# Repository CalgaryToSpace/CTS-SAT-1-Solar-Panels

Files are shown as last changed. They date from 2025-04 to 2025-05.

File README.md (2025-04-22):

# CTS-SAT-1-Solar-Panels
Solar panel PCB designs for the CTS-SAT-1 3U cubesat

## Overview
* 4x COTS 2U solar panels are the main power generation for the satellite.
* As a proof of concept, the following panels are manufactured in-house:
    * 2x 1.25U panels
    * 1x 1.0U panel
* Each panel has backflow blocking diodes and shadow-protection diodes.

## 1.25U Solar Panel

* 30 cells, in a 6S5P configuration (6 cells in each string, then joined in parallel).

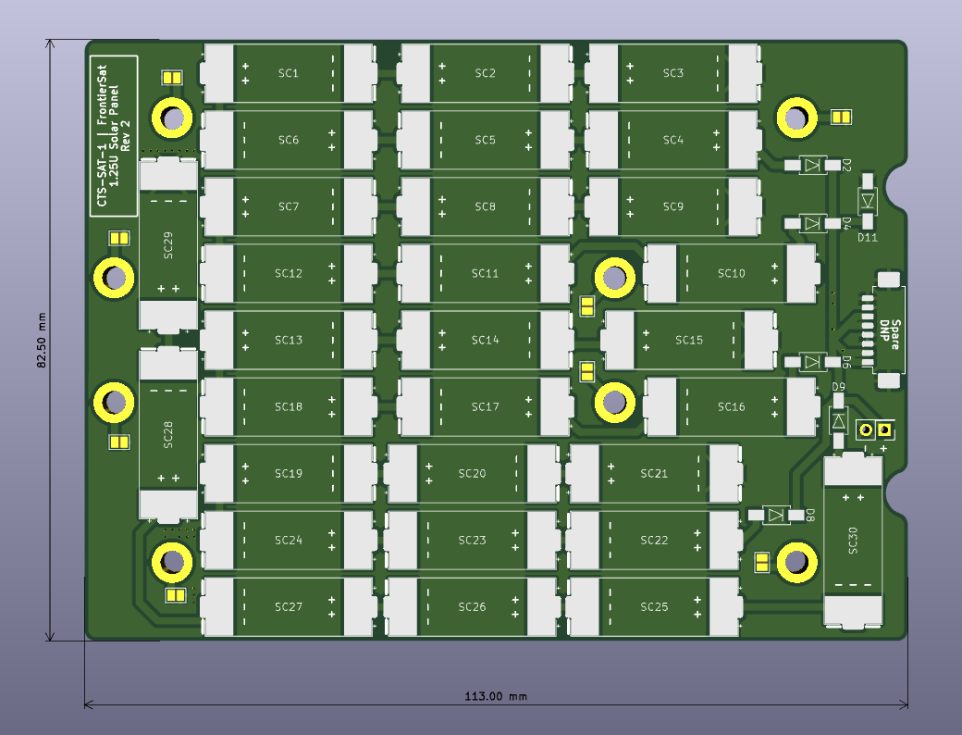
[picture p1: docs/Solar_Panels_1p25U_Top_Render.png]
1.25U Solar Panel - Top


## Bill of Materials
* PMEG10020AELPX diode in a SOD128 package
* [AA-DUCT 902 Silver Epoxy Adhesive](https://atomadhesives.com/aa-duct-902-silver-epoxy-adhesive-electrically-conductive-room-temp-curing-air-dr/)

## Solar Panel Assembly Steps
Work in the Laminar Flow Table with proper ESD protection. Wear gloves. Be careful with fragile cells.

1. Clean solar panel with isopropyl alcohol.
2. Boil some water.
3. Put epoxy in hot water for 10 minutes.
4. Massage epoxy in pouch.
5. Get out the solar cells.
6. Apply some epoxy to solar panel pads.
7. Take a picture of the application for reference on future applications.
8. Use the suction tool to place solar cells on the panels.
9. Apply pressure by placing a PCB on top of the soldered panel, and placing a 300g mass on top.
10. Wait 24h for epoxy to dry.
11. Solder short wires to the nearby pads, ensuring the solder blobs do not stick out the back side.
12. Inspect the work.
13. The assembly is complete. 

## License
This project is licensed under the [CERN OHL v2 Permissive](https://choosealicense.com/licenses/cern-ohl-p-2.0/) license. We appreciate attribution and links back, but you are free to do what you wish with this project.

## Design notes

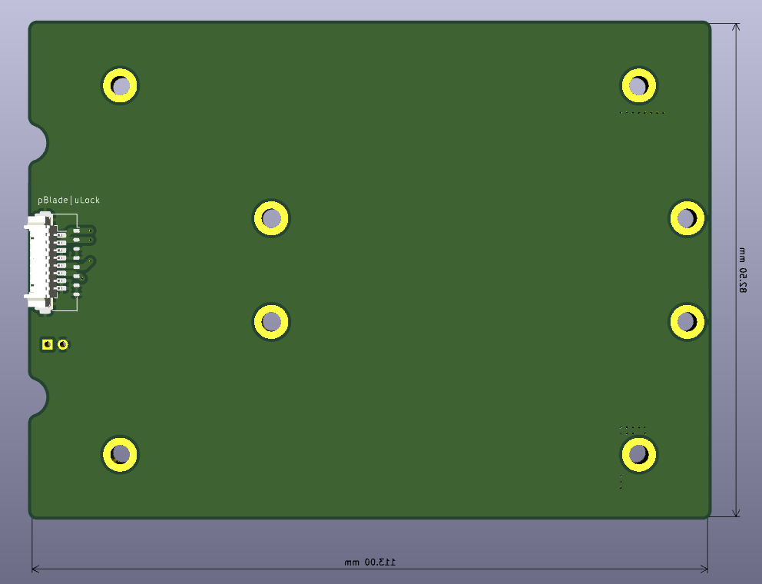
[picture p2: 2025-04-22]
docs/Solar_Panels_1p25U_Bottom_Render.png

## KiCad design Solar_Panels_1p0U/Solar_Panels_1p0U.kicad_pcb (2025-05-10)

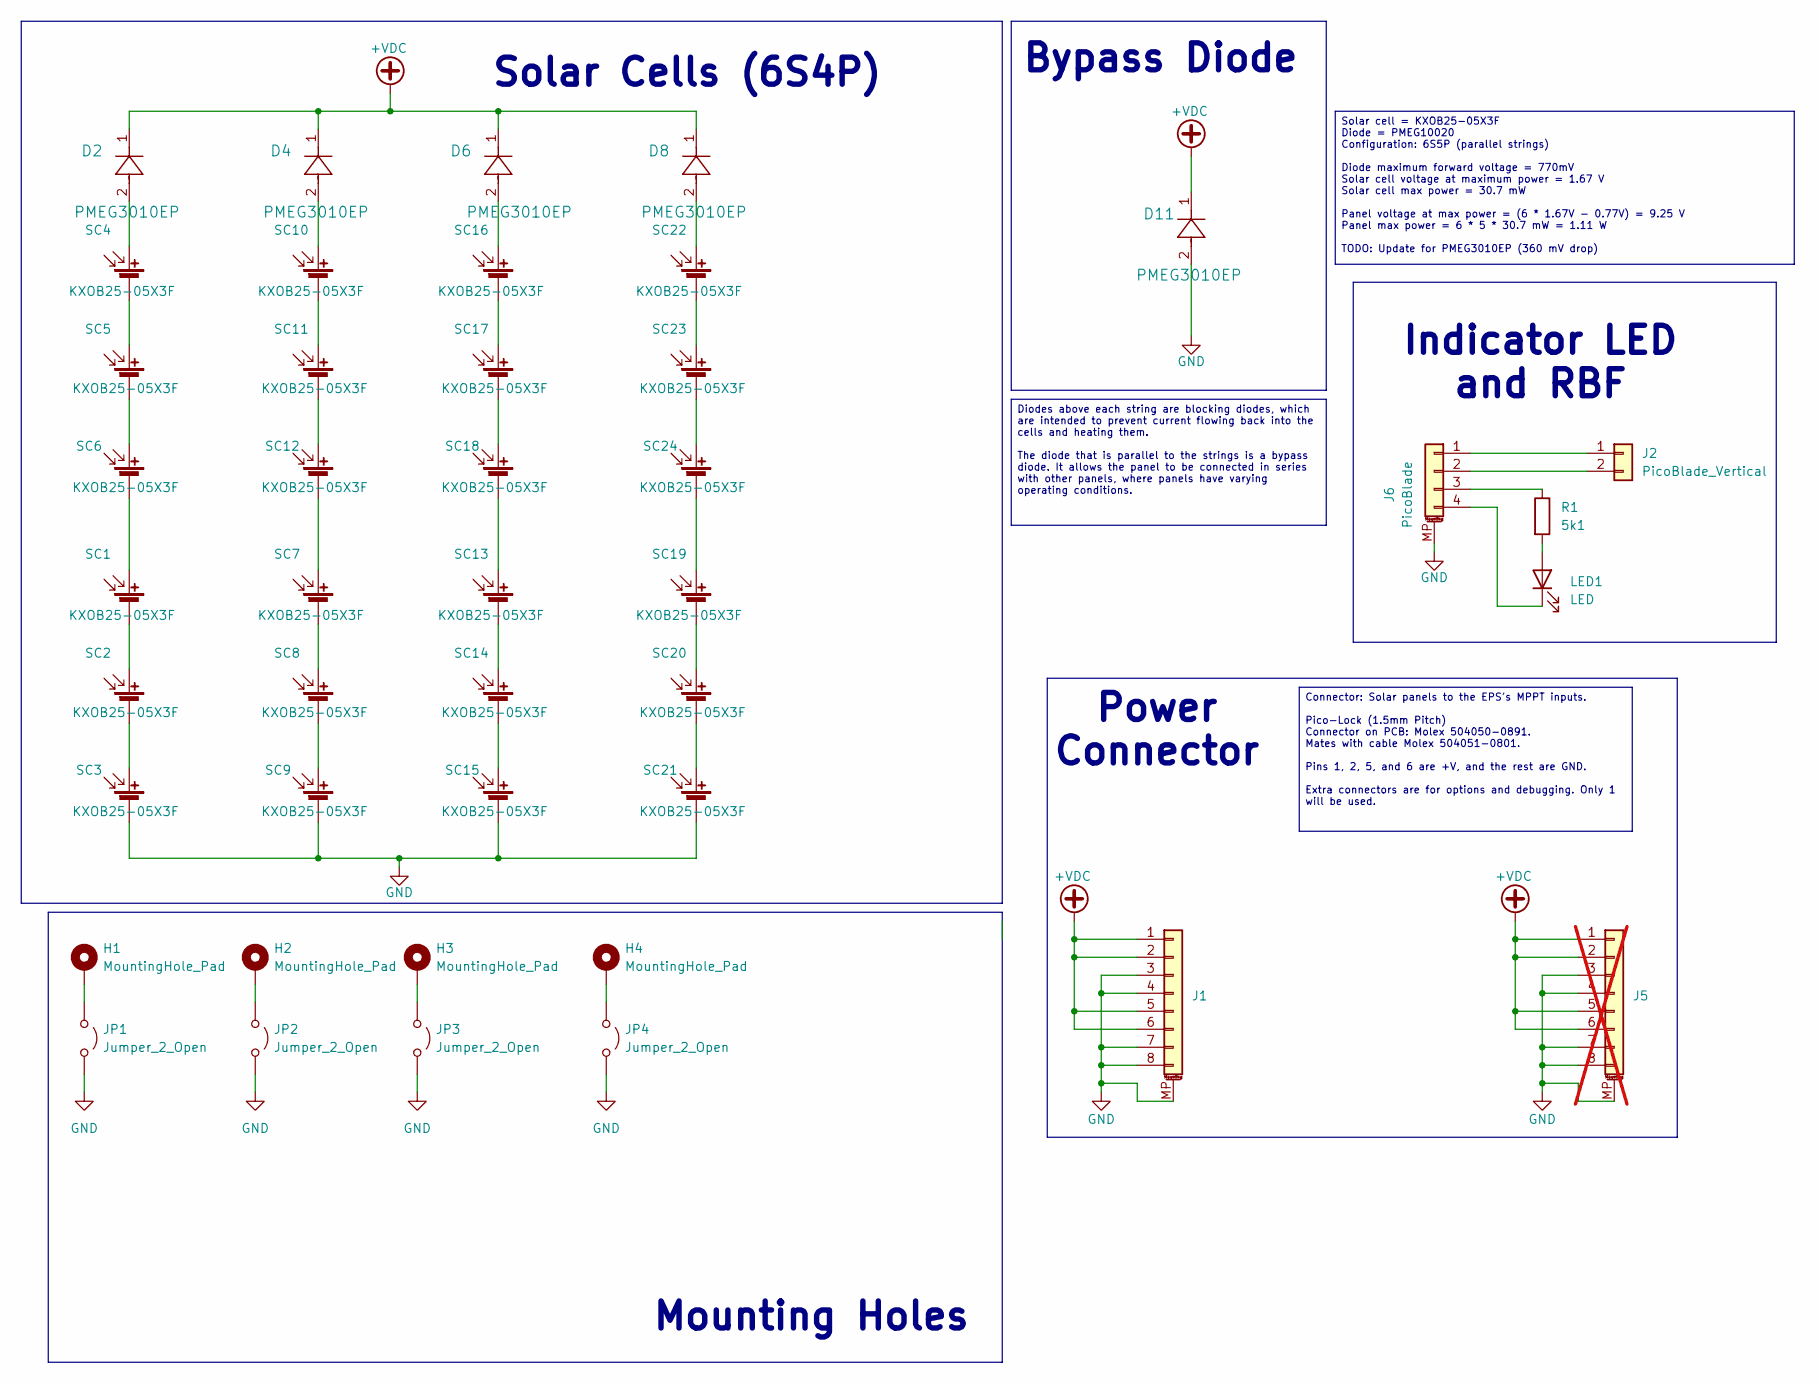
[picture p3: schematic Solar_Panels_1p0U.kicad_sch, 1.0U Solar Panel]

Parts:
D2, D4, D6, D8, D11: PMEG3010EP; PMEG10020AELPX
H1, H2, H3, H4: MountingHole_Pad; MountingHole_3.2mm_M3_DIN965_Pad
J1: Conn_01x08_MountingPin; Molex_PicoBlade_53261-0871_1x08-1MP_P1.25mm_Horizontal
J2: PicoBlade_Vertical; Molex_PicoBlade_53047-0210_1x02_P1.25mm_Vertical
J5: Conn_01x08_MountingPin; Molex_Pico-Lock_504050-0891_1x08-1MP_P1.50mm_Horizontal; not fitted
J6: PicoBlade; Molex_PicoBlade_53261-0471_1x04-1MP_P1.25mm_Horizontal
JP1, JP2, JP3, JP4: Jumper_2_Open; SolderJumper-2_P1.3mm_Open_Pad1.0x1.5mm
LED1: LED; LED_0603_1608Metric_Pad1.05x0.95mm_HandSolder
R1: 5k1; R_0603_1608Metric_Pad0.98x0.95mm_HandSolder
SC1, SC2, SC3, SC4, SC5, SC6, SC7, SC8, SC9, SC10, SC11, SC12, SC13, SC14, SC15, SC16, SC17, SC18, SC19, SC20, SC21, SC22, SC23, SC24: KXOB25-05X3F

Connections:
+VDC: D2.1, D4.1, D6.1, D8.1, D11.1, J1.1, J1.2, J1.5, J1.6, J5.1, J5.2, J5.5, J5.6
GND: D11.2, J1.3, J1.4, J1.7, J1.8, J1.MP (MountPin), J5.3, J5.4, J5.7, J5.8, J5.MP (MountPin), J6.MP (MountPin), JP1.2 (B), JP2.2 (B), JP3.2 (B), JP4.2 (B), SC3.2 (-), SC9.2 (-), SC15.2 (-), SC21.2 (-)
unnamed: J2.1, J6.1
unnamed: J2.2, J6.2
unnamed: J6.3, R1.1
unnamed: J6.4, LED1.1 (K)
unnamed: H1.1, JP1.1 (A)
unnamed: H2.1, JP2.1 (A)
unnamed: H3.1, JP3.1 (A)
unnamed: H4.1, JP4.1 (A)
unnamed: LED1.2 (A), R1.2
unnamed: SC1.1 (+), SC6.2 (-)
unnamed: SC1.2 (-), SC2.1 (+)
unnamed: SC2.2 (-), SC3.1 (+)
unnamed: D2.2, SC4.1 (+)
unnamed: SC4.2 (-), SC5.1 (+)
unnamed: SC5.2 (-), SC6.1 (+)
unnamed: SC7.2 (-), SC8.1 (+)
unnamed: SC8.2 (-), SC9.1 (+)
unnamed: D4.2, SC10.1 (+)
unnamed: SC10.2 (-), SC11.1 (+)
unnamed: SC11.2 (-), SC12.1 (+)
unnamed: SC7.1 (+), SC12.2 (-)
unnamed: SC13.1 (+), SC18.2 (-)
unnamed: SC13.2 (-), SC14.1 (+)
unnamed: SC14.2 (-), SC15.1 (+)
unnamed: D6.2, SC16.1 (+)
unnamed: SC16.2 (-), SC17.1 (+)
unnamed: SC17.2 (-), SC18.1 (+)
unnamed: SC19.1 (+), SC24.2 (-)
unnamed: SC19.2 (-), SC20.1 (+)
unnamed: SC20.2 (-), SC21.1 (+)
unnamed: D8.2, SC22.1 (+)
unnamed: SC22.2 (-), SC23.1 (+)
unnamed: SC23.2 (-), SC24.1 (+)

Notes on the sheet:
Power Connector
Mounting Holes
Bypass Diode
Indicator LED and RBF
Solar Cells (6S4P)
Diodes above each string are blocking diodes, which are intended to prevent current flowing back into the cells and heating them. The diode that is parallel to the strings is a bypass diode. It allows the panel to be connected in series with other panels, where panels have varying operating conditi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
Connector: Solar panels to the EPS's MPPT inputs. Pico-Lock (1.5mm Pitch) Connector on PCB: Molex 504050-0891. Mates with cable Molex 504051-0801. Pins 1, 2, 5, and 6 are +V, and the rest are GND. Extra connectors are for options and debugging. Only 1 will be used.
Solar cell = KXOB25-05X3F Diode = PMEG10020 Configuration: 6S5P (parallel strings) Diode maximum forward voltage = 770mV Solar cell voltage at maximum power = 1.67 V Solar cell max power = 30.7 mW Panel voltage at max power = (6 * 1.67V - 0.77V) = 9.25 V Panel max power = 6 * 5 * 30.7 mW = 1.11 W T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

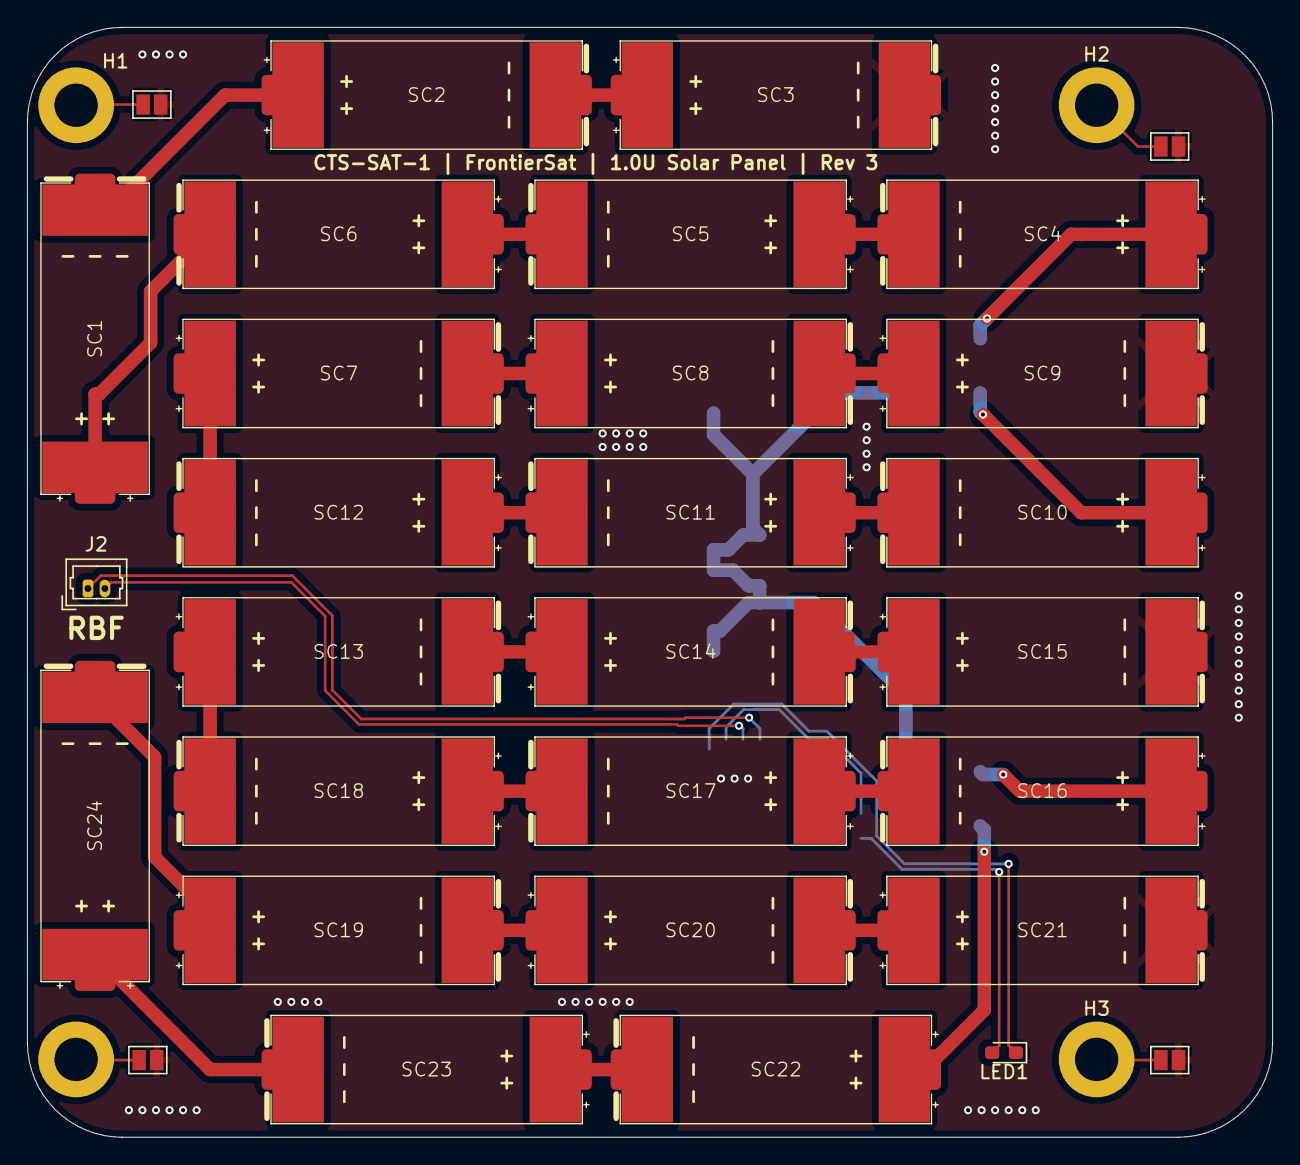
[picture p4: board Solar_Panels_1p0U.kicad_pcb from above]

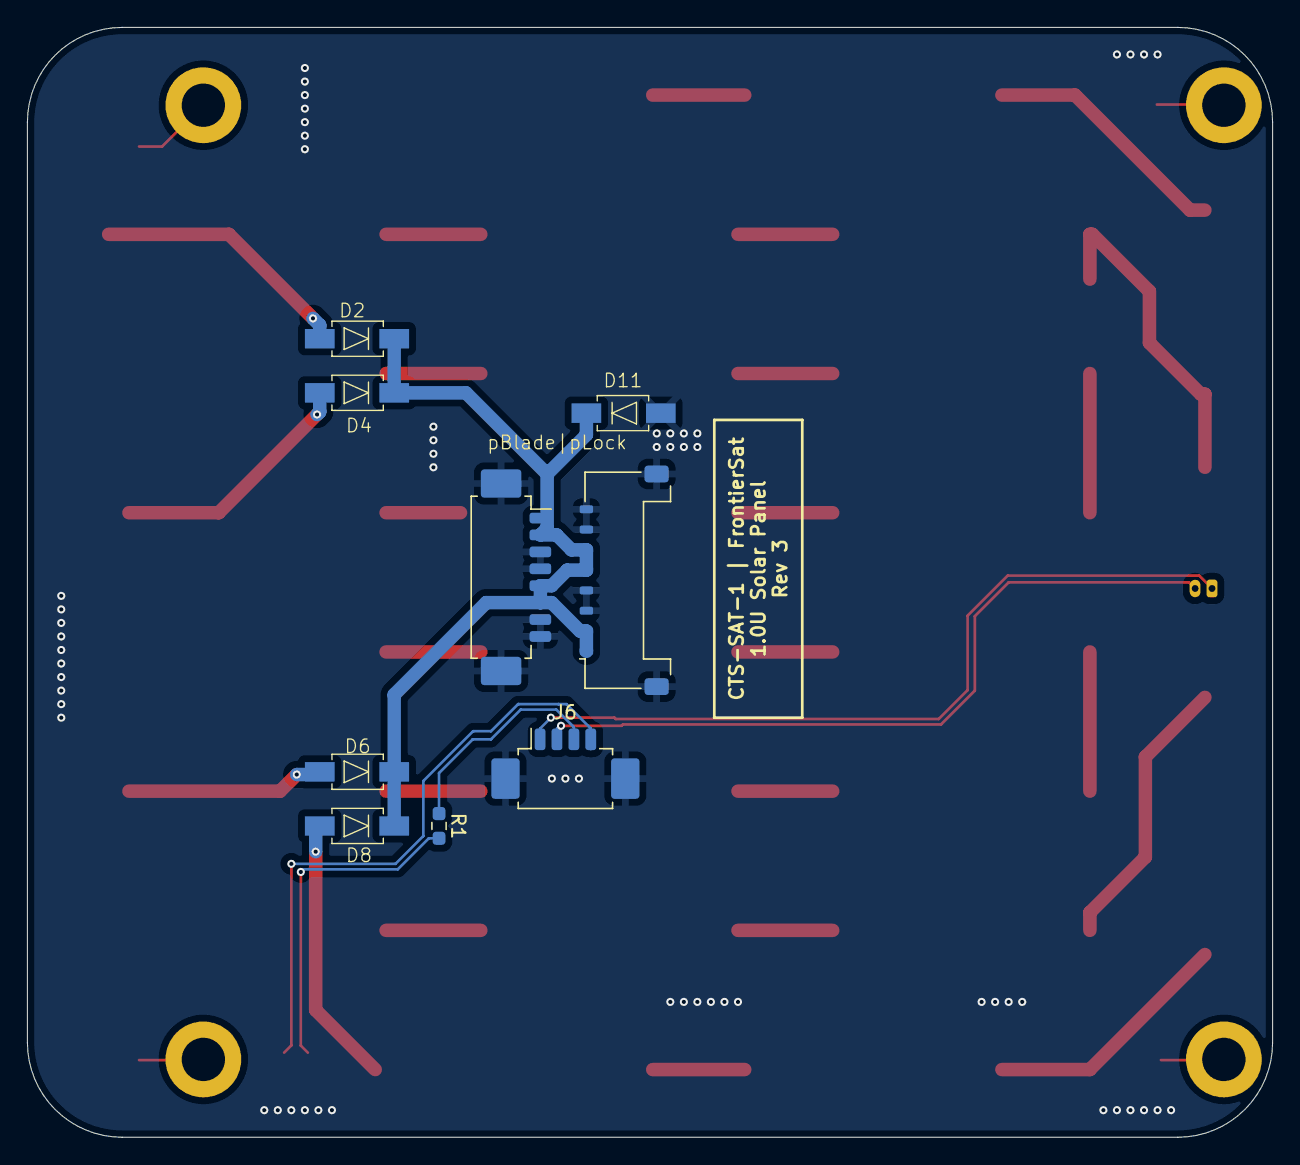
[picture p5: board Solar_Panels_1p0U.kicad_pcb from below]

Board: 2 copper layers, 92.0 x 82.0 mm, 43 parts (9 on the bottom side), 35 nets.

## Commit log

2024-01-16 Add a couple notes to README
2024-07-13 Add KiCAD Gitignore
2024-07-13 Initial Design
    Design before being revised by Parker and Dr. Nacho
    [Solar Panels.kicad_pcb, Solar Panels.kicad_sch]
2024-07-17 Updated Initial Panels
    Updated a bit of the routing before Parker and Nacho takes a look at it. Put the connector on the inside.
    [Solar Panels.kicad_pcb]
2024-07-17 Initial Panels Revision
    Changed the Solar Panels to adjust to structural needs.
    [Solar Panels.kicad_pcb]
2024-07-17 Updated Solar Panels
    Revised to fit Brett's preferences.
    [Solar Panels.kicad_pcb]
2024-07-24 Modifications For 2U Panels
    Made structural modifications to suit Brett's structure and tried to improve the PCB board based on Parker's suggestions. Schematic is extremely wonky right now but will try to fix it ASAP.
    [Solar Panels.kicad_pcb, Solar Panels.kicad_sch]
2024-07-30 Diodes changes and adjusted schematic.
    Made the diode changes based off Parker's suggestions and fixed the schematic. Comments are now included within the schematic.
    [Solar Panels.kicad_pcb, Solar Panels.kicad_sch]
2024-07-31 Quick Adjustments to Schematic and Routing
    Adjusted so there's only one bypass diode for the entire panel. Made changes to the routing as well.
    [Solar Panels.kicad_pcb, Solar Panels.kicad_sch]
2024-08-06 Routed the PCB after the Footprint Adjustments
    Routed the PCB after making adjustments to the TriSolX footprint.
    [Solar Panels.kicad_pcb, Solar Panels.kicad_sch]
2024-08-07 PDF Schematic
    Created a PDF Schematic for review.
2024-08-07 Added Vdc Info
    Quick schematic change to indicate vdc.
    [Solar Panels.kicad_sch]
2024-08-07 more information added to schematic
    added more info for the voltages
    [Solar Panels.kicad_sch]
2024-08-10 Refined Simons 2u
    I tried refining Simons design a bit and aligned the holes/dimensions to the most current frame version.
    Looking good on the structural side. Think we just need a last electrical review then should be ready to order.
    [Solar Panels.kicad_pcb]
2024-08-17 Small schematic cleanup
    [Solar Panels.kicad_sch]
2024-08-17 Improve footprints, layout, routing
    [Solar Panels.kicad_pcb, Solar Panels.kicad_sch]
2024-08-24 Changed the footprint of the solar panels a tiny bit
    Changed the footprints so that the keepout zone is a tiny bit bigger.
    [Solar Panels.kicad_pcb]
2024-08-24 Adjusted some placements and the footprint
    Made some adjustments to the footprint (changing placement of the throughhole and the placement of solar cells)
    [Solar Panels.kicad_pcb]
2024-08-25 Made adjustments to Trisolx footprint and rerouted
    [Solar Panels.kicad_pcb]
2024-08-27 Adjust layout, add back-side cross-board pour
    [Solar Panels.kicad_pcb]
2024-08-27 Add dimensioning drawings and comments
    [Solar Panels.kicad_pcb]
2024-08-28 Reorganize lib and rename project to Solar_Panels_1p25U
    [Solar_Panels_1p25U.kicad_pcb, Solar_Panels_1p25U.kicad_sch]
2024-08-28 Add diode name to README (#6)
2024-08-28 Create initial 1U revision (#7)
    * Started 1U Solar Panels Design
    Begun to start on the 1U design.
    * Schematic Finished for 1U Panel
    Title
    * August 20th Changes
    Finished setting up the PCB board (haven't started the PCB board yet)
    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
    [Solar_Panels_1p0U.kicad_pcb, Solar_Panels_1p0U.kicad_sch]
2024-08-28 Prep Rev 1 release
    [Solar_Panels_1p0U.kicad_pcb, Solar_Panels_1p0U.kicad_sch, Solar_Panels_1p25U.kicad_pcb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]
2025-04-19 Design new Rev 2 solar panel with new cells
    [Solar_Panels_1p25U.kicad_pcb, Solar_Panels_1p25U.kicad_sch]
2025-04-22 Finish routing
    [Solar_Panels_1p25U.kicad_pcb, Solar_Panels_1p25U.kicad_sch]
2025-04-22 Update footprints with extra protuding pads for testing
    [Solar_Panels_1p25U.kicad_pcb, Solar_Panels_1p25U.kicad_sch]
2025-04-22 Finalize Rev 2
    [Solar_Panels_1p25U.kicad_pcb]
2025-05-09 Update diode model and description
    [Solar_Panels_1p25U.kicad_sch]
2025-05-09 1.25U: Fix typo on connector label
    [Solar_Panels_1p25U.kicad_pcb]
2025-05-09 1.0U: Layout cells
    [Solar_Panels_1p0U.kicad_pcb, Solar_Panels_1p0U.kicad_sch]
2025-05-09 1.0U: Finalize layout mostly
    [Solar_Panels_1p0U.kicad_pcb, Solar_Panels_1p0U.kicad_sch]
2025-05-10 1.0U: More layout and routing
    [Solar_Panels_1p0U.kicad_pcb]
2025-05-10 Finish Rev 3 - 1.0U
    [Solar_Panels_1p0U.kicad_pcb, Solar_Panels_1p0U.kicad_sch]
2025-05-10 Finalize Rev 3 of both panels
    [Solar_Panels_1p0U.kicad_pcb, Solar_Panels_1p0U.kicad_sch, Solar_Panels_1p25U.kicad_pcb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]
2025-09-24 docs: clarify assembly and BOM in final CTS-SAT-1 assembly
